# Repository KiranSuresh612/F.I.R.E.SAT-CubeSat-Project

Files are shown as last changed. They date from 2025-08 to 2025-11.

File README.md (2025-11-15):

# F.I.R.E.SAT

### Building a 3U CubeSat to combat the spread of wildfires.

## TL;DR
F.I.R.E.SAT (Fire Intervention Rescue Expedition Satellite) is a student-led CubeSat concept designed to monitor and detect wildfires from low Earth orbit. This project adds detailed CAD Modelling in Autodesk Inventor with intense FEA Testing in Ansys to create a flight-ready satellite chassis. Additionally, a CNN was retrained in MATLAB to detect fires from an augmented dataset of terrestrial fires and achieved ~94% accuracy, which was then implemented into a pipeline created in Simulink to simulate downlinking logic from orbit. More details on F.I.R.E.SAT can be found below or in the various folders of this repo. Thank you for visiting!  

## Table of Contents
- [Introduction](#Introduction)
- [Motivation and Objective](#Motivation-and-Objective)
- [CAD Modelling](#CAD-Modelling)
- [FEA Testing](#FEA-Testing)
- [CNN Retraining](#CNN-Retraining)
- [Simulink Pipeline](#Simulink-Pipeline)
- [How to View and Use Files](#How-to-View-and-Use-Files)
- [Acknowledgements](#Acknowledgements)
- [Concluding Details](#Concluding-Details)
- [References](#References)

## Introduction
F.I.R.E.SAT (Fire Intervention Rescue Expedition Satellite) is a self-conducted project where I designed a 3U (10 cm x 10 cm x 30 cm) CubeSat that can withstand launch and low Earth orbit conditions, all while using a Convolutional Neural Network (CNN), retrained using augmented terrestrial pictures to detect fire signatures and downlink them using a Simulink pipeline. If this project were to be made and launched, the total cost to build, develop, and launch F.I.R.E.SAT would be about $400,000 USD, which is certainly not pocket money. However, feel free to explore this repo to learn more about F.I.R.E.SAT!

F.I.R.E.SAT Exploded View

## Motivation and Objective
Wildfires are a growing threat to ecosystems around the world, especially in Canada, with severe cases across the country. Current wildfire detection satellites cannot both rapidly detect and capture fine-resolution imagery to detect wildfires. The payload is a FLIR BOSON+ 640 Infrared Camera, which will perform better than most wildfire detection satellites today since infrared cameras perform better than regular cameras when the CubeSat is in Earth's shadow. Though F.I.R.E.SAT may not solve all the listed problems with modern satellites, I want it to be a mission-ready concept that, with more resources and development, may become a flight-ready mission that improves our wildfire detection and prevention capabilities. All concept sketches and art are under the "Preliminary Sketches and Designs" folder.

### CAD Modelling
The CAD model was developed in Autodesk Inventor using various industry-sourced components and several self-developed parts. The CubeSat model has the dimensions 9.8 cm x 9.8 cm x 30 cm and is 1:1 in scale. I did not make the side lengths 10 cm, as I wanted about 0.2 cm as clearance for the CubeSat launcher's deployer rails. To make my CAD model as accurate as possible, I got CAD models from the vendors themselves. These components are: (NanoMind A3200), Power System (NanoPower P60), Comms (NanoCom AX100), Docking System (NanoDock DMC-3), GPS Kit (NanoSense NovAtel OEM-719), Thermal Camera (FLIR BOSON+ 640 with a 73mm lens), Star Trackers (AAC Hyperion ST200), Sun Sensors (AAC Hyperion SS200), Battery (AAC Clyde Space Optimus 30-Watt Battery). I created several parts as well, such as most of the Attitude Determination and Control System or ADCS (controls the orientation of the satellite in space) shown below, the Antennae Deployer, all Mainframe parts, Protective Germanium Lens (to shield the thermal sensor from space), and Solar Cells. 

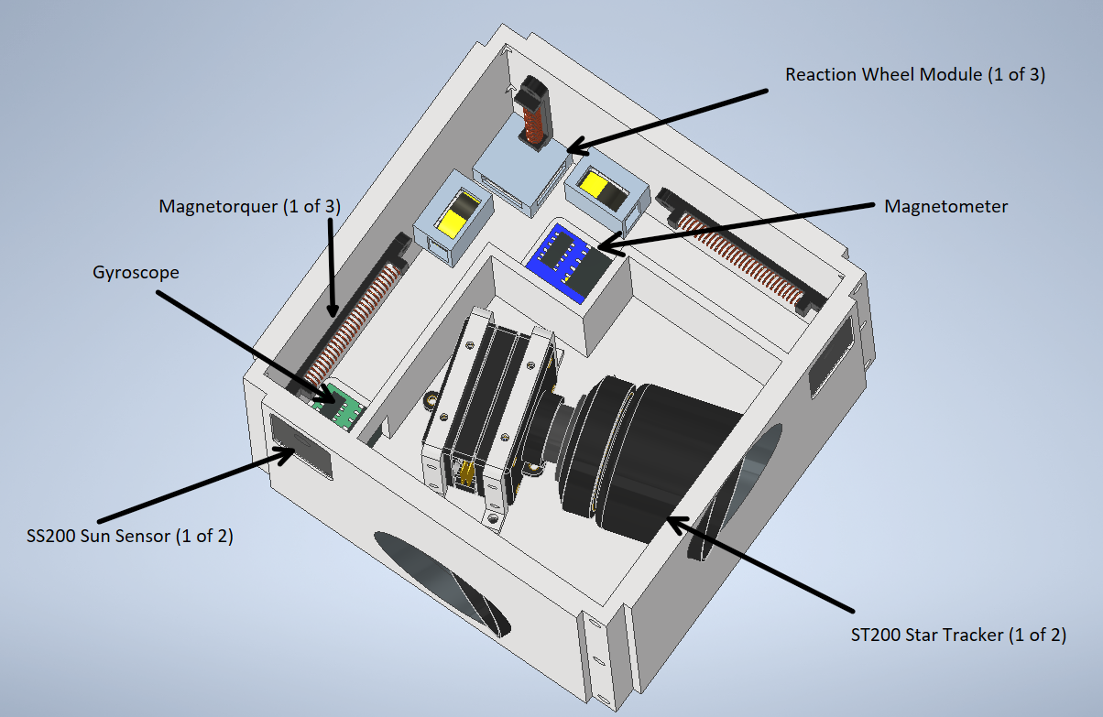
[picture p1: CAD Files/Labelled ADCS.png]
Labelled Diagram of the ADCS


By gathering CAD models of flight-proven components from vendors, I was able to devote more time to the structure/mainframe of F.I.R.E.SAT to make it more rigid and stable. The system layout is one aspect I am very proud of, as they are placed in such a manner that their respective abilities are optimized. For example, the battery is placed farthest from the thermal sensor and ADCS to prevent the heat from those components from reaching the battery, since the battery requires a strict temperature range between 30 and 50 degrees Celsius. Another example would be the placement of the ADCS system, as it is placed close to the satellite's center of mass, allowing for better attitude control. 

I often wanted to add several components to F.I.R.E.SAT, but had to hold myself back because it would not fit within my mainframe design. The CAD model allowed me to explore my vision for F.I.R.E.SAT and helped establish trade-offs between functionality and factors like weight and volume.

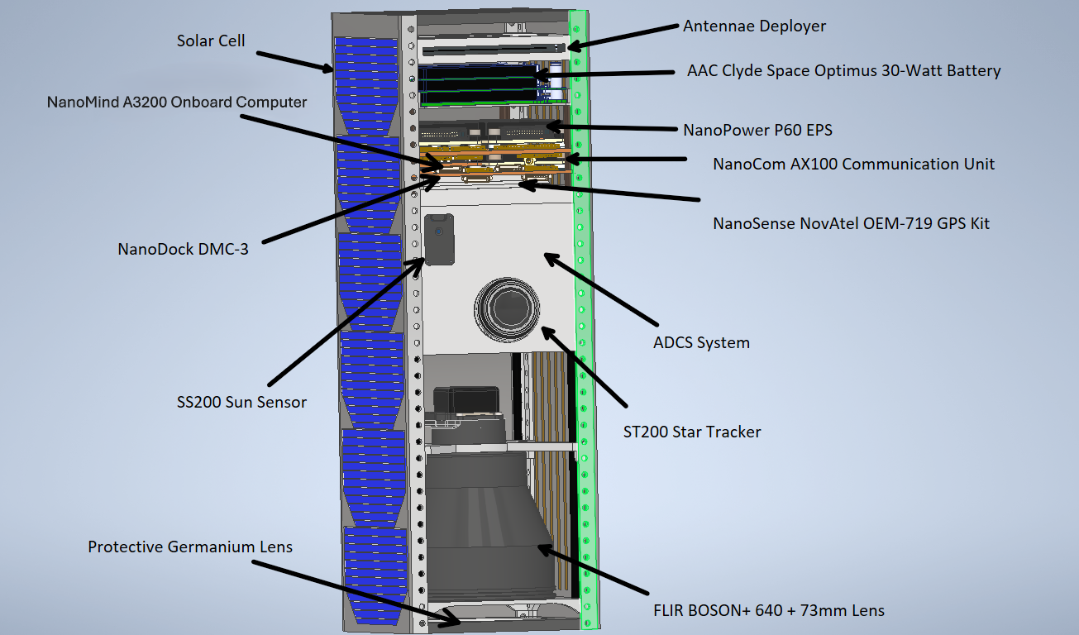
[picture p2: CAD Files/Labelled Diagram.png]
Labelled Diagram of F.I.R.E.SAT


### FEA Testing
To test if the satellite would survive under launch and orbital conditions, Finite Element Analysis (FEA) was conducted on the model. FEA is the process of breaking complex structures into tiny parts called finite elements and then applying specific conditions to those elements to test how the entire structure behaves. I assigned Aluminum 6061-T6 to be the material for my CubeSat mainframe and exterior because it is commonly used in satellite structures, and then conducted three tests: Deformation, Modal Frequency, and Transient Thermal. The Deformation and Modal Frequency tests were specifically designed to mimic launch conditions (i.e. when the satellite is brought up to space in a rocket). The tests were only done on the exterior walls and mainframe, since having the interior components built would create an unstable mesh, which couldn't be properly tested.  

In the Deformation tests, I installed a fixed support only to the bottom plate and applied 10Gs of force onto the entire structure from the X, Y, and Z axes to ensure the satellite would survive in all orientations. From the tests, the plate holding the battery faced the most deformation, which was not a lot either (~8.44e-6 m). To calculate the strain on the thinnest part of the plate (0.2 cm), we use the formula: deformation/length => 8.44e-6/0.002 => 4.22e-3%. This strain is well within the elastic limit for Aluminum 6061-T6, so it is negligible.

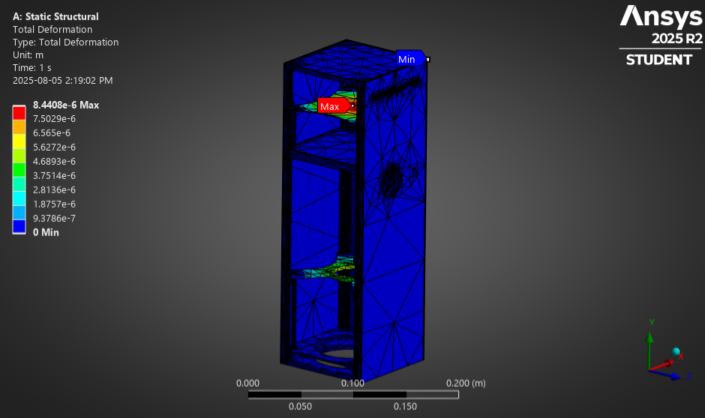
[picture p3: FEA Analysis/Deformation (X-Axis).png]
Deformation X-Axis


In the Modal Frequency (Max Vibration before the structure collapses) test, it was found that the max modal frequency of F.I.R.E.SAT's exterior and mainframe was about 655 Hz, which is well above the minimum 100 Hz requirement imposed by launch operators such as SpaceX. Even if I added the internal components, the modal frequency might drop to around 300 Hz (being harsh), which is still above the minimum frequency.

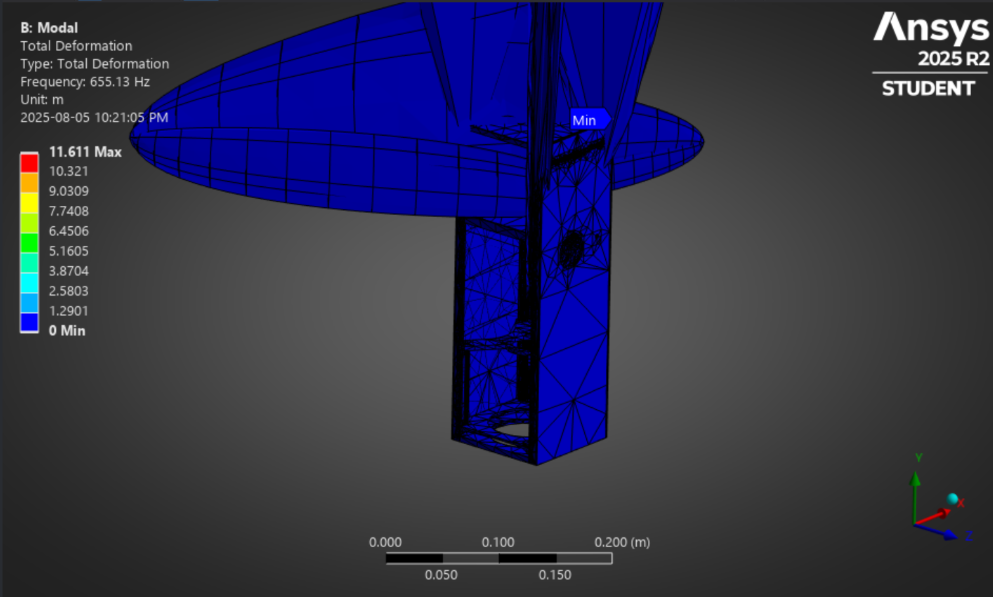
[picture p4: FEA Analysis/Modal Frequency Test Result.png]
Modal Frequency

NOTE: The model in the picture is distorted as it shows how the components WANT to move when subjected to force, but ACTUALLY will not. 

In the Transient Thermal (how temperature affects a body over time) test, I checked if the satellite would remain in its Goldilocks zone of 30-50 degrees Celsius during its 90-minute orbit around Earth. In its orbit, F.I.R.E.SAT would spend 45 minutes in sunlight and 45 minutes in shadow, so it would need to withstand a maximum temperature of 260 degrees Celsius and a minimum temperature of -100 degrees Celsius. The test showed temperatures between ~21 and 45 degrees Celsius on the exterior and 26 to 44 degrees Celsius inside the satellite. I also calculated the minimum radiator area using the Stefan-Boltzmann Law, finding that an area of at least 194 cm^2 needs to be dedicated to radiators to dissipate 9.5 W, the average power usage. I decided to allocate 277 cm^2 of radiator area, providing a 70% safety margin so the radiators can dissipate up to 13.5 W during peak operation (i.e. when everything inside the satellite, including heaters, is running). Below is a GIF of the Transient Thermal test running:

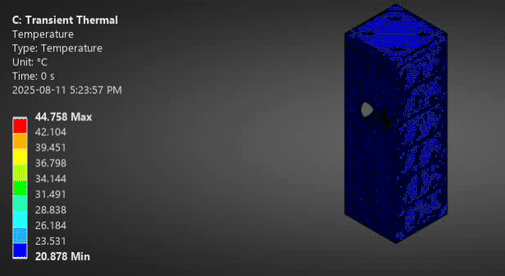
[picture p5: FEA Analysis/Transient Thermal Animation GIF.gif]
Transient Thermal GIF


More Test Results can be viewed in the "FEA Analysis" folder!

### CNN Retraining
I retrained the pre-existing Convolutional Neural Network (CNN), SqueezeNet, to detect fire signatures using a dataset containing terrestrial fire images in .png format compiled by a team of researchers at Mendeley Data (citation in References) in MATLAB. SqueezeNet was chosen due to its low hardware requirements, which is a constant constraint in CubeSats such as F.I.R.E.SAT. The training set consisted of two folders, each containing thousands of pictures of either fires or no fires. These pictures were augmented to challenge the CNN and reduce the chances of the CNN memorizing the images instead of learning to differentiate between the two classes. These augmentations consisted of resizing, random rotations, and translations, which greatly helped the CNN generalize (i.e. make it adaptable so it can detect fires in any set of pictures instead of just the training set). 

During training, a set of images was fed alongside the training set, called the validation set, to see if the CNN was memorizing images and measure its learning after each epoch (i.e. each loop of the training set). After training, the model was tested on classifying a brand new set of images called the testing dataset, where the retrained model achieved an accuracy of ~94%! Though this is a great result, a part of me wishes I were able to use .HDF files containing thermal imagery from real satellite data to retrain the CNN, which would make it very close to being mission-ready. However, I am still proud of my progress and am very glad I took on this challenge to learn more about AI applications in wildfire detection. Below are the training progress graphs and the confusion matrix, which organizes the predictions of the CNN during testing.

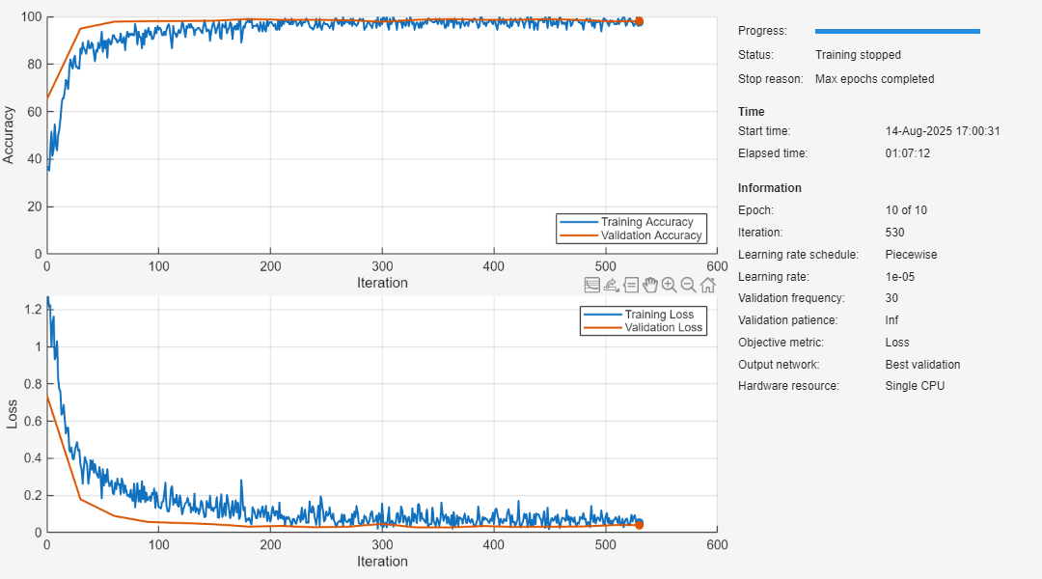
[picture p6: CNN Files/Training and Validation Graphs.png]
Training and Validation Graphs


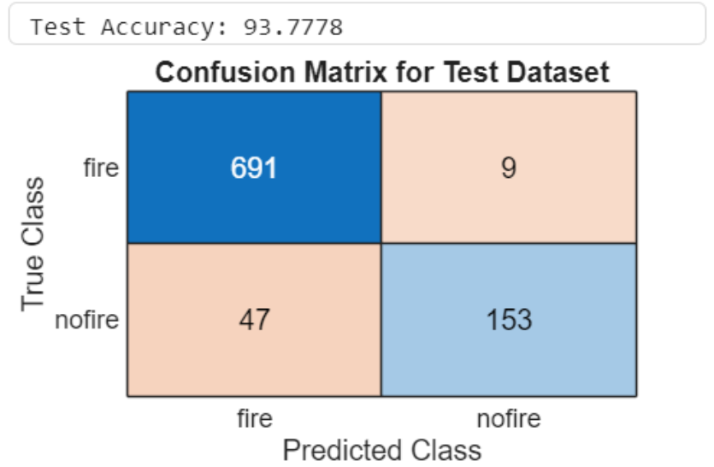
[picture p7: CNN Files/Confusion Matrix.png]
Confusion Matrix


### Simulink Pipeline
The pipeline created in Simulink was made to complement the retrained CNN by simulating how F.I.R.E.SAT handles wildfire imaging and processing in orbit, with the only constraint in this simulation being a limited battery power. The process starts with an image being captured and preprocessed for image classification by the CNN. After classification, the CNN outputs the prediction on whether the image contains a fire or not and a percentage to show how confident it is in its prediction. The prediction enters a stateflow chart meant to be a downlink logic box with three states: Idle, ReadyToTransmit, and LowBattery. The prediction is passed through (i.e. approved for being sent down to Earth) if and only if a fire has been detected and there is sufficient charge in the battery. This measure is to reduce the volume of data sent down to Earth and automate the process of pinpointing the locations of fires. 

The battery factor was included to simulate how the satellite downlinking logic should react at different battery levels to either send data of detected fires immediately or send the last reading, then enter Safe Mode to preserve the satellite for future use instead of entirely using it up and potentially missing fires along the line. One thing I wanted to figure out was how to feed a folder of images instead of one image at a time to test the downlink logic under more realistic circumstances.

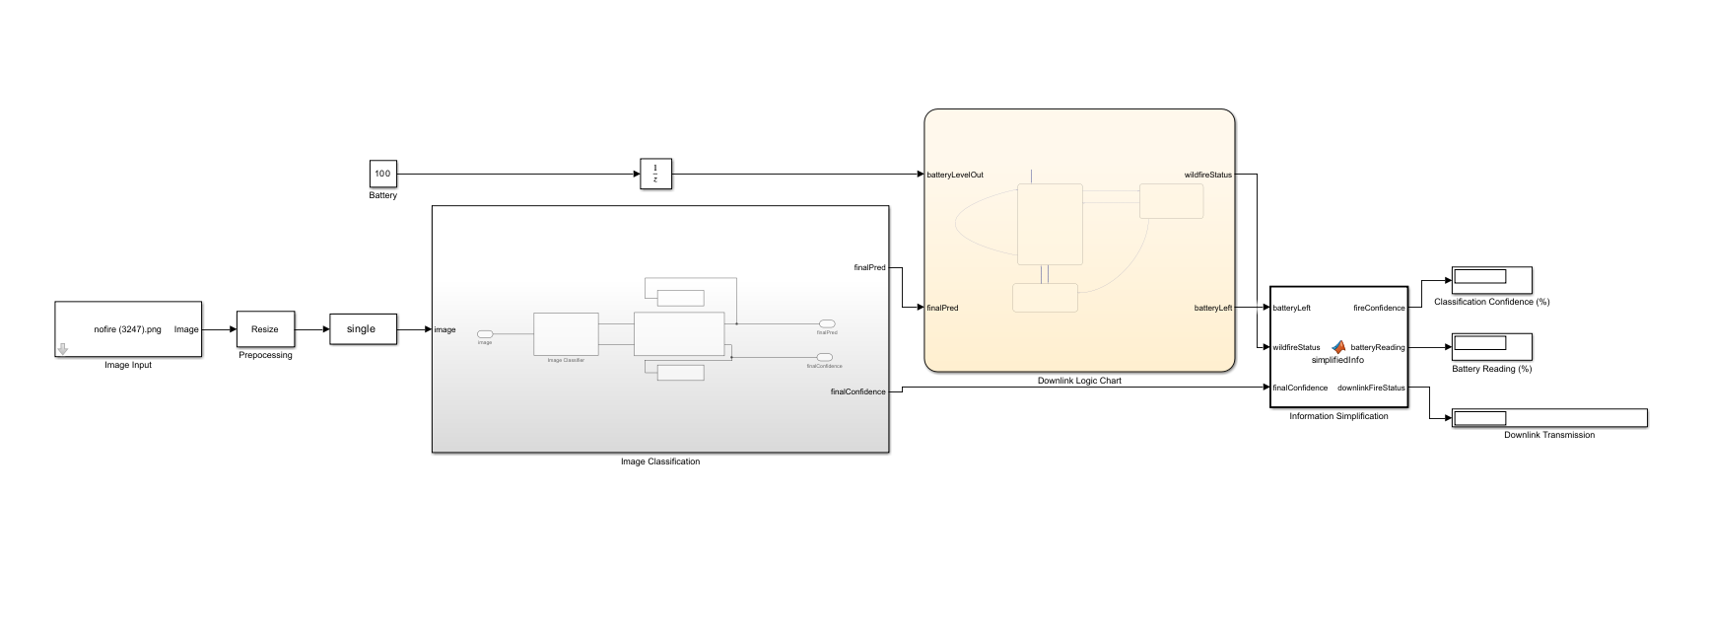
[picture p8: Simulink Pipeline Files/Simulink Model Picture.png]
Simulink Pipeline Picture


## How to View and Use Files

If you would like to go through my work on F.I.R.E.SAT, feel free to do so via the various folders of this repo. If you are having trouble, please take a look at the instructions below.

CAD Model: 
Go to the "CAD Files" folder, download the file named "F.I.R.E.SAT Mk.2 (Final Design).iam" and open with a CAD-friendly software like SolidWorks, Autodesk Inventor, etc (preferably Autodesk Inventor).

NOTE: I used Autodesk Inventor 2025, so I cannot guarantee that the file will open at the time of download.

FEA Workflow: 
Go to the "FEA Analysis" folder, download the file named "FEA Model.wbpj" and open it with Ansys Workbench. The workflow and the used model are already in the workbench file! 

NOTE: I used Ansys Workbench/Mechanical 2025 R2 (Student Version), so I don't know if the Workbench file will behave the same for you when you download it.

CNN Retraining: 
Download the dataset by following the link in the References section and extract all the files. Please note that you will be using the folders in the Classification folder. Then, go to the "CNN Files" folder, download the file named "Training Script.m" and open it in MATLAB. Fill in the sections listed in the code and finally run. Make sure all the files you download and use are in the same folder. It will take a varying amount of time to train (depends on your specs) and then test, but after that, you will have your very own retrained wildfire detection CNN. 

NOTE: I used MATLAB R2025a, so I do not know if the syntax or script will still work at the time of download. I also had to download the Deep Learning Toolbox and the Statistics and Machine Learning Toolbox (not 100% sure if needed by install just in case) using the Add-On explorer. 

Simulink Pipeline: 
Go to the "Simulink Pipeline Files" folder, download the files named "simulink_OBC_Diagram.slx" and "simulink_OBC_Diagram.slxc" and save them to the same folder. Then, transfer a copy of your retrained CNN from the folder you used for MATLAB (previous activity) to your newly made folder. Also, be sure to have a folder containing a few images from the dataset mentioned previously (fire and no fire samples) in the same primary folder. Then insert the file path of a sample of your choosing into the field given by double-clicking the Image Input box (farthest left). Then hit Run to see the results on the displays to the far right of the model. Be sure to test with both types of samples and by tweaking the battery level (small white box with 100) to a number between 1 and 100 of your choosing while also being to enter the same number in the "Initial Condition" field in the other small white box to the right of the battery box (denoted with a 1/z). 

NOTE: I used Simulink R2025a, so I cannot confirm if my model still works at the time of download. I also downloaded Stateflow, Computer Vision Toolbox, and Image Processing Toolbox, so you may need to as well if the model does not run properly. 

## Acknowledgements
I want to extend a deep appreciation to GomSpace, TELEDYNE, and AAC Clyde Space for allowing me to use their CAD files for their company's components in my project. It made the design process infinitely easier with their help. This project is not to be used for commercial purposes unless permission is gained from all three entities.

To gain the skills necessary to work on the tasks I wanted to in this project, I often used MathWorks courses such as Deep Learning Onramp and Stateflow Onramp. If you have access to them, they are extremely useful and also provide a digital certificate.

Software Used: Autodesk Inventor 2025, Ansys Workbench/Mechanical 2025 R2 (Student Version), MATLAB R2025a, Simulink R2025a

## Concluding Details

You made it to the end of the README file! Congratulations! Or you could have skipped down here; either way, thank you for taking the time to look through the project that took two months of pure dedication and grit! If you would like to work together on improving F.I.R.E.SAT or want to contact me for other purposes, please do so with the contact details listed on my profile. Thank you, and have a great day!

## References

Database Citation: Ibn Jafar, Anam; Islam, Al Mohimanul ; Binta Masud, Fatiha; Ullah, Jeath Rahmat; Ahmed, Md. Rayhan (2023), “FlameVision : A new dataset for wildfire classification and detection using aerial imagery ”, Mendeley Data, V4, doi: 10.17632/fgvscdjsmt.4 (Link: https://data.mendeley.com/datasets/fgvscdjsmt/4)

NASA's CubeSAT 101: Basic Concepts and Processes for First-Time CubeSat Developers NASA CubeSat Launch Initiative. (n.d.). https://www.nasa.gov/wp-content/uploads/2017/03/nasa_csli_cubesat_101_508.pdf?emrc=05d3e2

Youtube Videos: The Efficient Engineer. (2024, May 21). How to Build a Satellite. YouTube. https://www.youtube.com/watch?v=5voQfQOTem8

Mark Rober. (2024, November 29). My New Satellite Can Take Your Selfie From Space. YouTube. https://www.youtube.com/watch?v=6KcV1C1Ui5s‌

‌

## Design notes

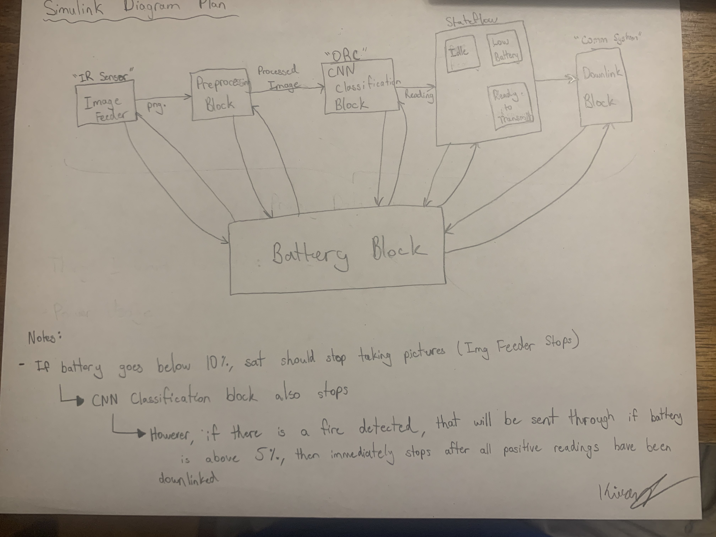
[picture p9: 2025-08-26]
Preliminary Sketches and Designs/Simulink Preliminary Diagram Design.jpeg

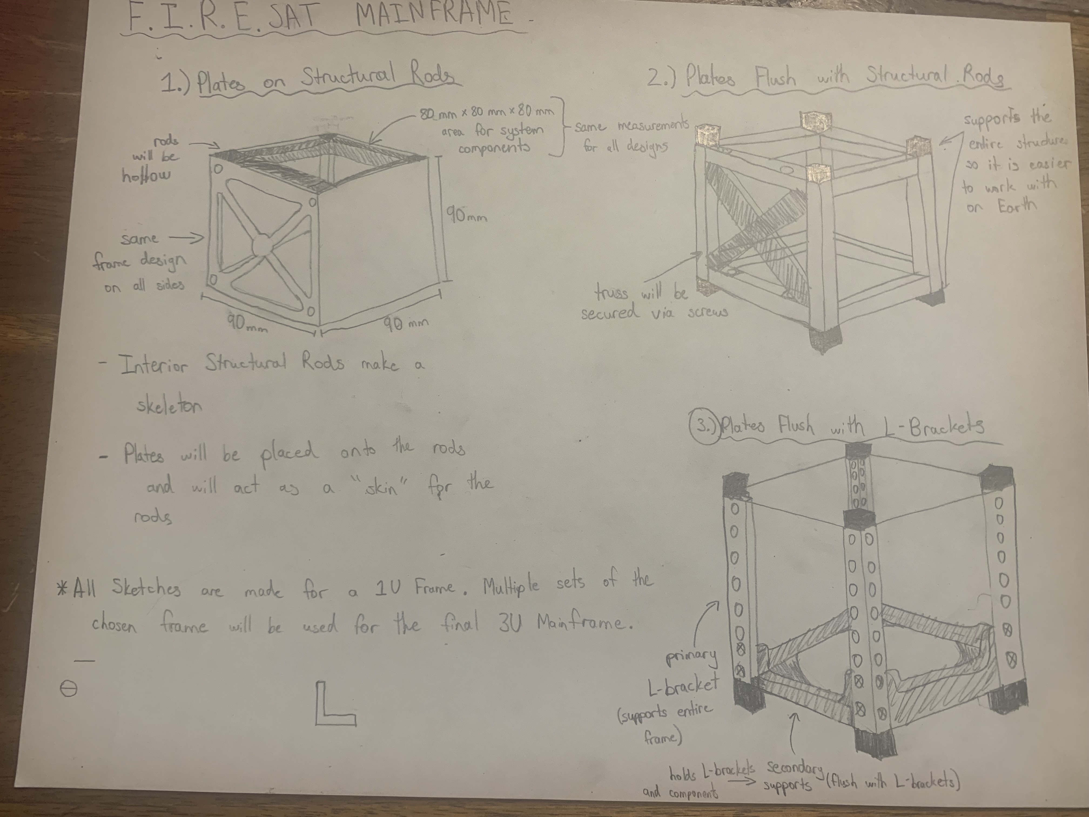
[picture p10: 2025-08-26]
Preliminary Sketches and Designs/Mainframe Preliminary Annotated Design.jpeg

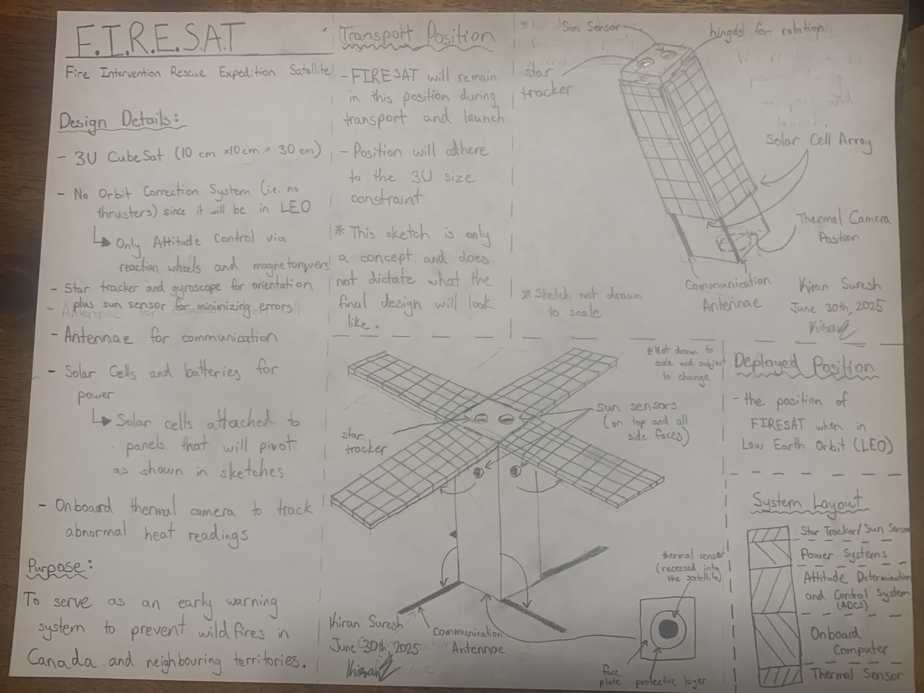
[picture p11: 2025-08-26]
Preliminary Sketches and Designs/FIRESAT Preliminary Annotated Design.jpeg

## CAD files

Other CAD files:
CAD Files/Modal Analysis CAD.iam

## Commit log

2025-08-24 Exploded View Video of CAD Model
    This video showcases the exploded view of the F.I.R.E.SAT CAD model, showing how all core subsystems fit together to make the nanosatellite function.
2025-08-24 Animated Exploded View of CAD Model
    In this GIF, you can view the various parts and subsystems used to create F.I.R.E.SAT and how they fit together to make a nanosatellite.
2025-08-26 CAD file
2025-08-26 added CAD files
    [Modal Analysis CAD.iam]
